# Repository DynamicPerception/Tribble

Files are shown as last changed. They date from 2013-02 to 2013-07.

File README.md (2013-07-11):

Tribble Board
=============

Tribble is the core PCB in the MX3 Motion Controller.

Key Features
------------

 * AT90USB1287 processor with USB OTG
 * 5-Button Interface
 * 2x16 LCD display
 * Dual-optocoupled outputs via 1x TRS jack
 * Four auxiliary I/O ports via 2x TRS jacks
 * MoCoBus Interface
 * Multiple Power Source Inputs

Author
------

The Tribble board was designed and created by Parker Dillmann (longhornengineer)

License and Copyright
---------------------

Tribble and the MX3 are Copyright (c) 2012-2013 Dynamic Perception LLC.

All files shared under the Creative Commons Attibution-Share-Alike 3.0 License.

Tribble and MX3 names are trademarks of Dynamic Perception LLC.

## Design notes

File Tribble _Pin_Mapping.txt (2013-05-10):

MX-3 Pin Mapping 
AT90USB646

0	PA0		M0_A
1	PA1		M0_B
2	PA2		M0_P
3	PA3		M1_A
4	PA4		M1_B
5	PA5		M1_P
6	PA6		M2_A
7	PA7		M2_B

8	PB0		M2_P
9	PB1		SCK
10	PB2		MOSI
11	PB3		MISO
12	PB4		COM1
13	PB5		SHT
14	PB6		N/a
15	PB7		FOC

16	PC0		LCD_D4
17	PC1		LCD_D5
18	PC2		LCD_D6
19	PC3		LCD_D7
20	PC4		LCD_E
21	PC5		LCD_RS
22	PC6		LCD_BK
23	PC7		N/a

24	PD0		COM3
25	PD1		COM2
26	PD2		RX
27	PD3		TX
28	PD4		DE
29	PD5		N/a
30	PD6		N/a
31	PD7		N/a

32	PE0		IO_3
33	PE1		N/a
34	PE2		N/a
35	PE3		OTG USB
36	PE4		IO_0
37	PE5		IO_1
38	PE6		IO_2
39	PE7		UVCON

40	PF0		BTNS
41	PF1		CUR_SENSOR
42	PF2		VOL_SENSOR
43	PF3		TEMP2_SENSOR
44	PF4		TEMP1_SENSOR
45	PF5		TEMP0_SENSOR
46	PF6		N/a
47	PF7		N/a

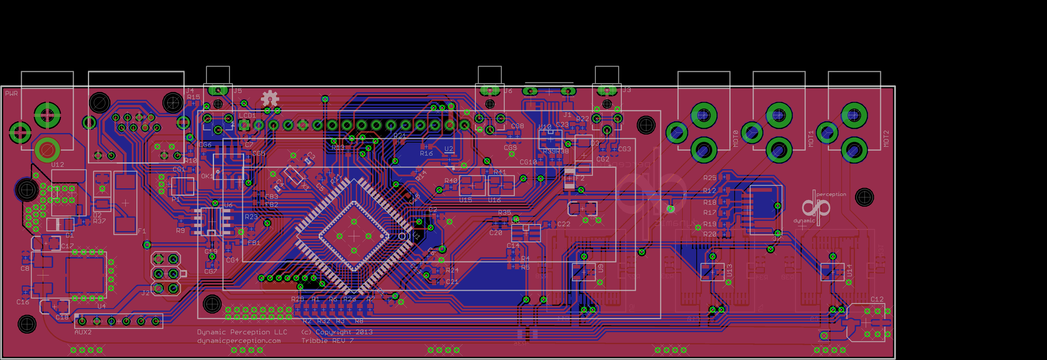
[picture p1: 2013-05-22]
Layout.png

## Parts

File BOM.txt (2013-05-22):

Partlist

Exported from Tribble.sch at 5/22/2013 1:43:17 PM

EAGLE Version 6.2.0 Copyright (c) 1988-2012 CadSoft

Assembly variant: 

Part     Value                    Device                          Package                Library               Sheet

AUX2                              PH_1X06SMALL_PTH                HEADER_01X06_SMALL_PTH PP_Connectors         1
C1       .1uF                     CAP_NONPOL0402                  0402_CAP               parkers_parts         1
C2       .1uF                     CAP_NONPOL0402                  0402_CAP               parkers_parts         1
C3       6pF                      CAP0402                         C0402                  SparkFun              1
C4       6pF                      CAP0402                         C0402                  SparkFun              1
C5       .1uF                     CAP_NONPOL0402                  0402_CAP               parkers_parts         1
C6       .1uF                     CAP_NONPOL0402                  0402_CAP               parkers_parts         1
C7       .1uF                     CAP_NONPOL0402                  0402_CAP               parkers_parts         1
C8       .1uF 35V                 CAP_NONPOL0402                  0402_CAP               parkers_parts         1
C9       .1uF 35V                 CAP_NONPOL0402                  0402_CAP               parkers_parts         1
C10      .1uF 35V                 CAP_NONPOL0402                  0402_CAP               parkers_parts         1
C11      .1uF 35V                 CAP_NONPOL0402                  0402_CAP               parkers_parts         1
C12      100uF                    CAPACITOR_POLARIZED6.3MM_SMD    6.3MM_CAP_SMD          PP_Passives           1
C13      .1uF                     CAP_NONPOL0402                  0402_CAP               parkers_parts         1
C14      .1uF                     CAP_NONPOL0402                  0402_CAP               parkers_parts         1
C15      1uF                      CAP_NONPOL0402                  0402_CAP               parkers_parts         1
C16      .1uF                     CAP_NONPOL0402                  0402_CAP               parkers_parts         1
C17      2.2uF                    CAP_POL1206                     EIA3216                SparkFun              1
C18      10uF                     CAP_POL1206                     EIA3216                SparkFun              1
C19      .1uF                     CAP_NONPOL0402                  0402_CAP               parkers_parts         1
C20      .1uF                     CAP_NONPOL0402                  0402_CAP               parkers_parts         1
C21      .1uF                     CAP_NONPOL0402                  0402_CAP               parkers_parts         1
C22      .1uF                     CAP_NONPOL0402                  0402_CAP               parkers_parts         1
C23      .1uF                     CAP_NONPOL0402                  0402_CAP               parkers_parts         1
C24      10uF                     CAP_POL1206                     EIA3216                SparkFun              1
CG1      B72590D50H260            RESISTOR0402                    0402_RES               parkers_parts         1
CG2      B72590D50H260            RESISTOR0402                    0402_RES               parkers_parts         1
CG3      B72590D50H260            RESISTOR0402                    0402_RES               parkers_parts         1
CG4      B72590D50H260            RESISTOR0402                    0402_RES               parkers_parts         1
CG5      B72590D50H260            RESISTOR0402                    0402_RES               parkers_parts         1
CG6      B72590D50H260            RESISTOR0402                    0402_RES               parkers_parts         1
CG7      B72590D50H260            RESISTOR0402                    0402_RES               parkers_parts         1
CG8      B72590D50H260            RESISTOR0402                    0402_RES               parkers_parts         1
CG9      B72590D50H260            RESISTOR0402                    0402_RES               parkers_parts         1
CG10     B72590D50H260            RESISTOR0402                    0402_RES               parkers_parts         1
D1       MMSZ5240C-V-GS08         DIODESOD-123                    SOD-123                parkers_parts         1
D2       PMEG6010EP,115           DIODESOD-128                    SOD-128                parkers_parts         1
D3       PMEG6010EP,115           DIODESOD-128                    SOD-128                PP_Passives           1
F1       MF-SM050-2-99            PTC_FUSE2920                    2920                   PP_Passives           1
F2       1206L025YR               PTC_FUSE1206                    1206                   PP_Passives           1
FB1      LI0402C470R-10           RESISTOR0402                    0402_RES               parkers_parts         1
FB2      LI0402C470R-10           RESISTOR0402                    0402_RES               parkers_parts         1
FB3      LI0402C470R-10           RESISTOR0402                    0402_RES               parkers_parts         1
J1       10118193-0001LF          USB10118193-0001LF              10118193-0001LF        PP_Connectors         1
J2       68602-406HLF             P2X03                           P2X03                  parkers_parts         1
J3       SJ1-2503A                TRS_STEREO_JACKSJ1-2503A        SJ1-2503A              parkers_parts         1
J4       RJHSE-5381               RJHS-538X                       RIGHT_ANGLE            amphenol ethernet     1
J5       SJ1-2503A                TRS_STEREO_JACKSJ1-2503A        SJ1-2503A              parkers_parts         1
J6       SJ1-2503A                TRS_STEREO_JACKSJ1-2503A        SJ1-2503A              parkers_parts         1
J7       HFW6R-2STE1LF            PH_1X06FFC                      HFW6R-2STE1LF          PP_Connectors         1
LCD1     LCD-16X2NOHOLES          LCD-16X2NOHOLES                 LCD-16X2_NOHOLES       SparkFun-Displays     1
MOT0     KLDX-0202-B-LT           DC_JACKPTH_TIGHT                DC_JACK_PTH_TIGHT      PP_Connectors         1
MOT1     KLDX-0202-B-LT           DC_JACKPTH_TIGHT                DC_JACK_PTH_TIGHT      PP_Connectors         1
MOT2     KLDX-0202-B-LT           DC_JACKPTH_TIGHT                DC_JACK_PTH_TIGHT      PP_Connectors         1
OK1      ACPL-227                 ACPL-227                        SOIC8                  avago-opto            1
P1       TC33X-2                  TC33X-2                         3MMSMD                 bourns trimpot        1
PWR      KLDX-0202-A-LT           DC_JACKPTH_TIGHT                DC_JACK_PTH_TIGHT      PP_Connectors         1
R1       4.7K                     RESISTOR0402                    0402_RES               parkers_parts         1
R2       4.7K                     RESISTOR0402                    0402_RES               parkers_parts         1
R3       4.7K                     RESISTOR0402                    0402_RES               parkers_parts         1
R4       4K                       RESISTOR0402                    0402_RES               parkers_parts         1
R5       20K                      RESISTOR0402                    0402_RES               parkers_parts         1
R6       4.7K                     RESISTOR0402                    0402_RES               parkers_parts         1
R7       4.7K                     RESISTOR0402                    0402_RES               parkers_parts         1
R8       4.7K                     RESISTOR0402                    0402_RES               parkers_parts         1
R9       120                      RESISTOR0402                    0402_RES               parkers_parts         1
R10      330                      RESISTOR0402                    0402_RES               parkers_parts         1
R11      10K                      RESISTOR0402                    0402_RES               parkers_parts         1
R12      500                      RESISTOR0402                    0402_RES               parkers_parts         1
R13      100                      RESISTOR0402                    0402_RES               parkers_parts         1
R14      5K                       RESISTOR0402                    0402_RES               parkers_parts         1
R15      330                      RESISTOR0402                    0402_RES               parkers_parts         1
R16      100                      RESISTOR0402                    0402_RES               parkers_parts         1
R17      500                      RESISTOR0402                    0402_RES               parkers_parts         1
R18      500                      RESISTOR0402                    0402_RES               parkers_parts         1
R19      500                      RESISTOR0402                    0402_RES               parkers_parts         1
R20      500                      RESISTOR0402                    0402_RES               parkers_parts         1
R21      2.6K                     RESISTOR0402                    0402_RES               parkers_parts         1
R22      0                        RESISTOR0402                    0402_RES               parkers_parts         1
R23      5K                       RESISTOR0402                    0402_RES               parkers_parts         1
R24      0                        RESISTOR0402                    0402_RES               parkers_parts         1
R25      10K                      RESISTOR0402                    0402_RES               parkers_parts         1
R26      4.7K                     RESISTOR0402                    0402_RES               parkers_parts         1
R27      10K                      RESISTOR0805                    0805                   PP_Passives           1
R28      10K                      RESISTOR0805                    0805                   PP_Passives           1
R29      4.7K                     RESISTOR0402                    0402_RES               parkers_parts         1
R30      10K                      RESISTOR0805                    0805                   PP_Passives           1
R31      10K                      RESISTOR0805                    0805                   PP_Passives           1
R32      4.7K                     RESISTOR0402                    0402_RES               parkers_parts         1
R33      10K                      RESISTOR0805                    0805                   PP_Passives           1
R34      10K                      RESISTOR0805                    0805                   PP_Passives           1
R35      20K                      RESISTOR0402                    0402_RES               parkers_parts         1
R36      LRF1206-LF-R006JT        RESISTOR1206                    1206                   PP_Passives           1
R37      10K                      RESISTOR0402                    0402_RES               parkers_parts         1
R38      22                       RESISTOR0402                    0402_RES               parkers_parts         1
R39      22                       RESISTOR0402                    0402_RES               parkers_parts         1
R40      100K                     RESISTOR0402                    0402_RES               parkers_parts         1
R41      10K                      RESISTOR0402                    0402_RES               parkers_parts         1
U1       AT90USB1287-MU           AT90USB647-MU                   MLF64                  at90usb               1
U2       MMDT3904                 MMDT3904                        SOT363                 SparkFun-DiscreteSemi 1
U3       BTM7755                  BTM7755PG-DSO-36-29             PG-DSO-36-29           PP_PowerIC            1
U4       MC78M05CDTG              FIXED_VOLTAGE_REGDPAK-3         DPAK-3                 PP_PowerIC            1
U5                                BTM7755PG-DSO-36-29             PG-DSO-36-29           PP_PowerIC            1
U6       ISL8483                  SN65176D                        SO-08                  texas                 1
U7                                BTM7755PG-DSO-36-29             PG-DSO-36-29           PP_PowerIC            1
U8       LMP8640MK-F/NOPB         LMP8640TSOT-6                   TSOT-6                 PP_AnalogIC           1
U9       MCP9701T-E/TT            MCP970XSOT-23-3                 SOT-23-3               PP_Sensors            1
U10      IP4234CZ6                IP4234CZ6SOT-457                SOT-457                PP_Passives           1
U11      AT90USB1287-AU           AT90USB647-AU                   TQFP64                 at90usb               1
U12      FDS6679AZ                MOSFET_P-CHANNEL_SINGLEP3-POWER DSO-8                  PP_DiscreteSemi       1
U13      MCP9701T-E/TT            MCP970XSOT-23-3                 SOT-23-3               PP_Sensors            1
U14      MCP9701T-E/TT            MCP970XSOT-23-3                 SOT-23-3               PP_Sensors            1
U15      BC847BMTF                BJT_NPN_SINGLESOT-23            SOT-23                 PP_DiscreteSemi       1
U16      FDV304P                  MOSFET_P-CHANNEL_SINGLESOT-23   SOT-23                 PP_DiscreteSemi       1
X1       TSX-3225 16.0000MF10U-B0 3.2X2.5MMCRYSTAL                3.2X2.5MM              kyocera-crystals      1

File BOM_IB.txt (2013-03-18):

Partlist

Exported from Input_Board.sch at 3/18/2013 1:31:10 PM

EAGLE Version 6.2.0 Copyright (c) 1988-2012 CadSoft

Assembly variant: 

Part     Value          Device         Package       Library              Sheet

J1       HFW6R-2STE1LF  PH_1X06FFC     HFW6R-2STE1LF PP_Connectors        1
SW1      EVQ-Q2203W     SPSTEVQ-Q2203W EVQ-Q2203W    PP_Electromechanical 1
SW2      EVQ-Q2203W     SPSTEVQ-Q2203W EVQ-Q2203W    PP_Electromechanical 1
SW3      EVQ-Q2203W     SPSTEVQ-Q2203W EVQ-Q2203W    PP_Electromechanical 1
SW4      EVQ-Q2203W     SPSTEVQ-Q2203W EVQ-Q2203W    PP_Electromechanical 1
SW5      EVQ-Q2203W     SPSTEVQ-Q2203W EVQ-Q2203W    PP_Electromechanical 1

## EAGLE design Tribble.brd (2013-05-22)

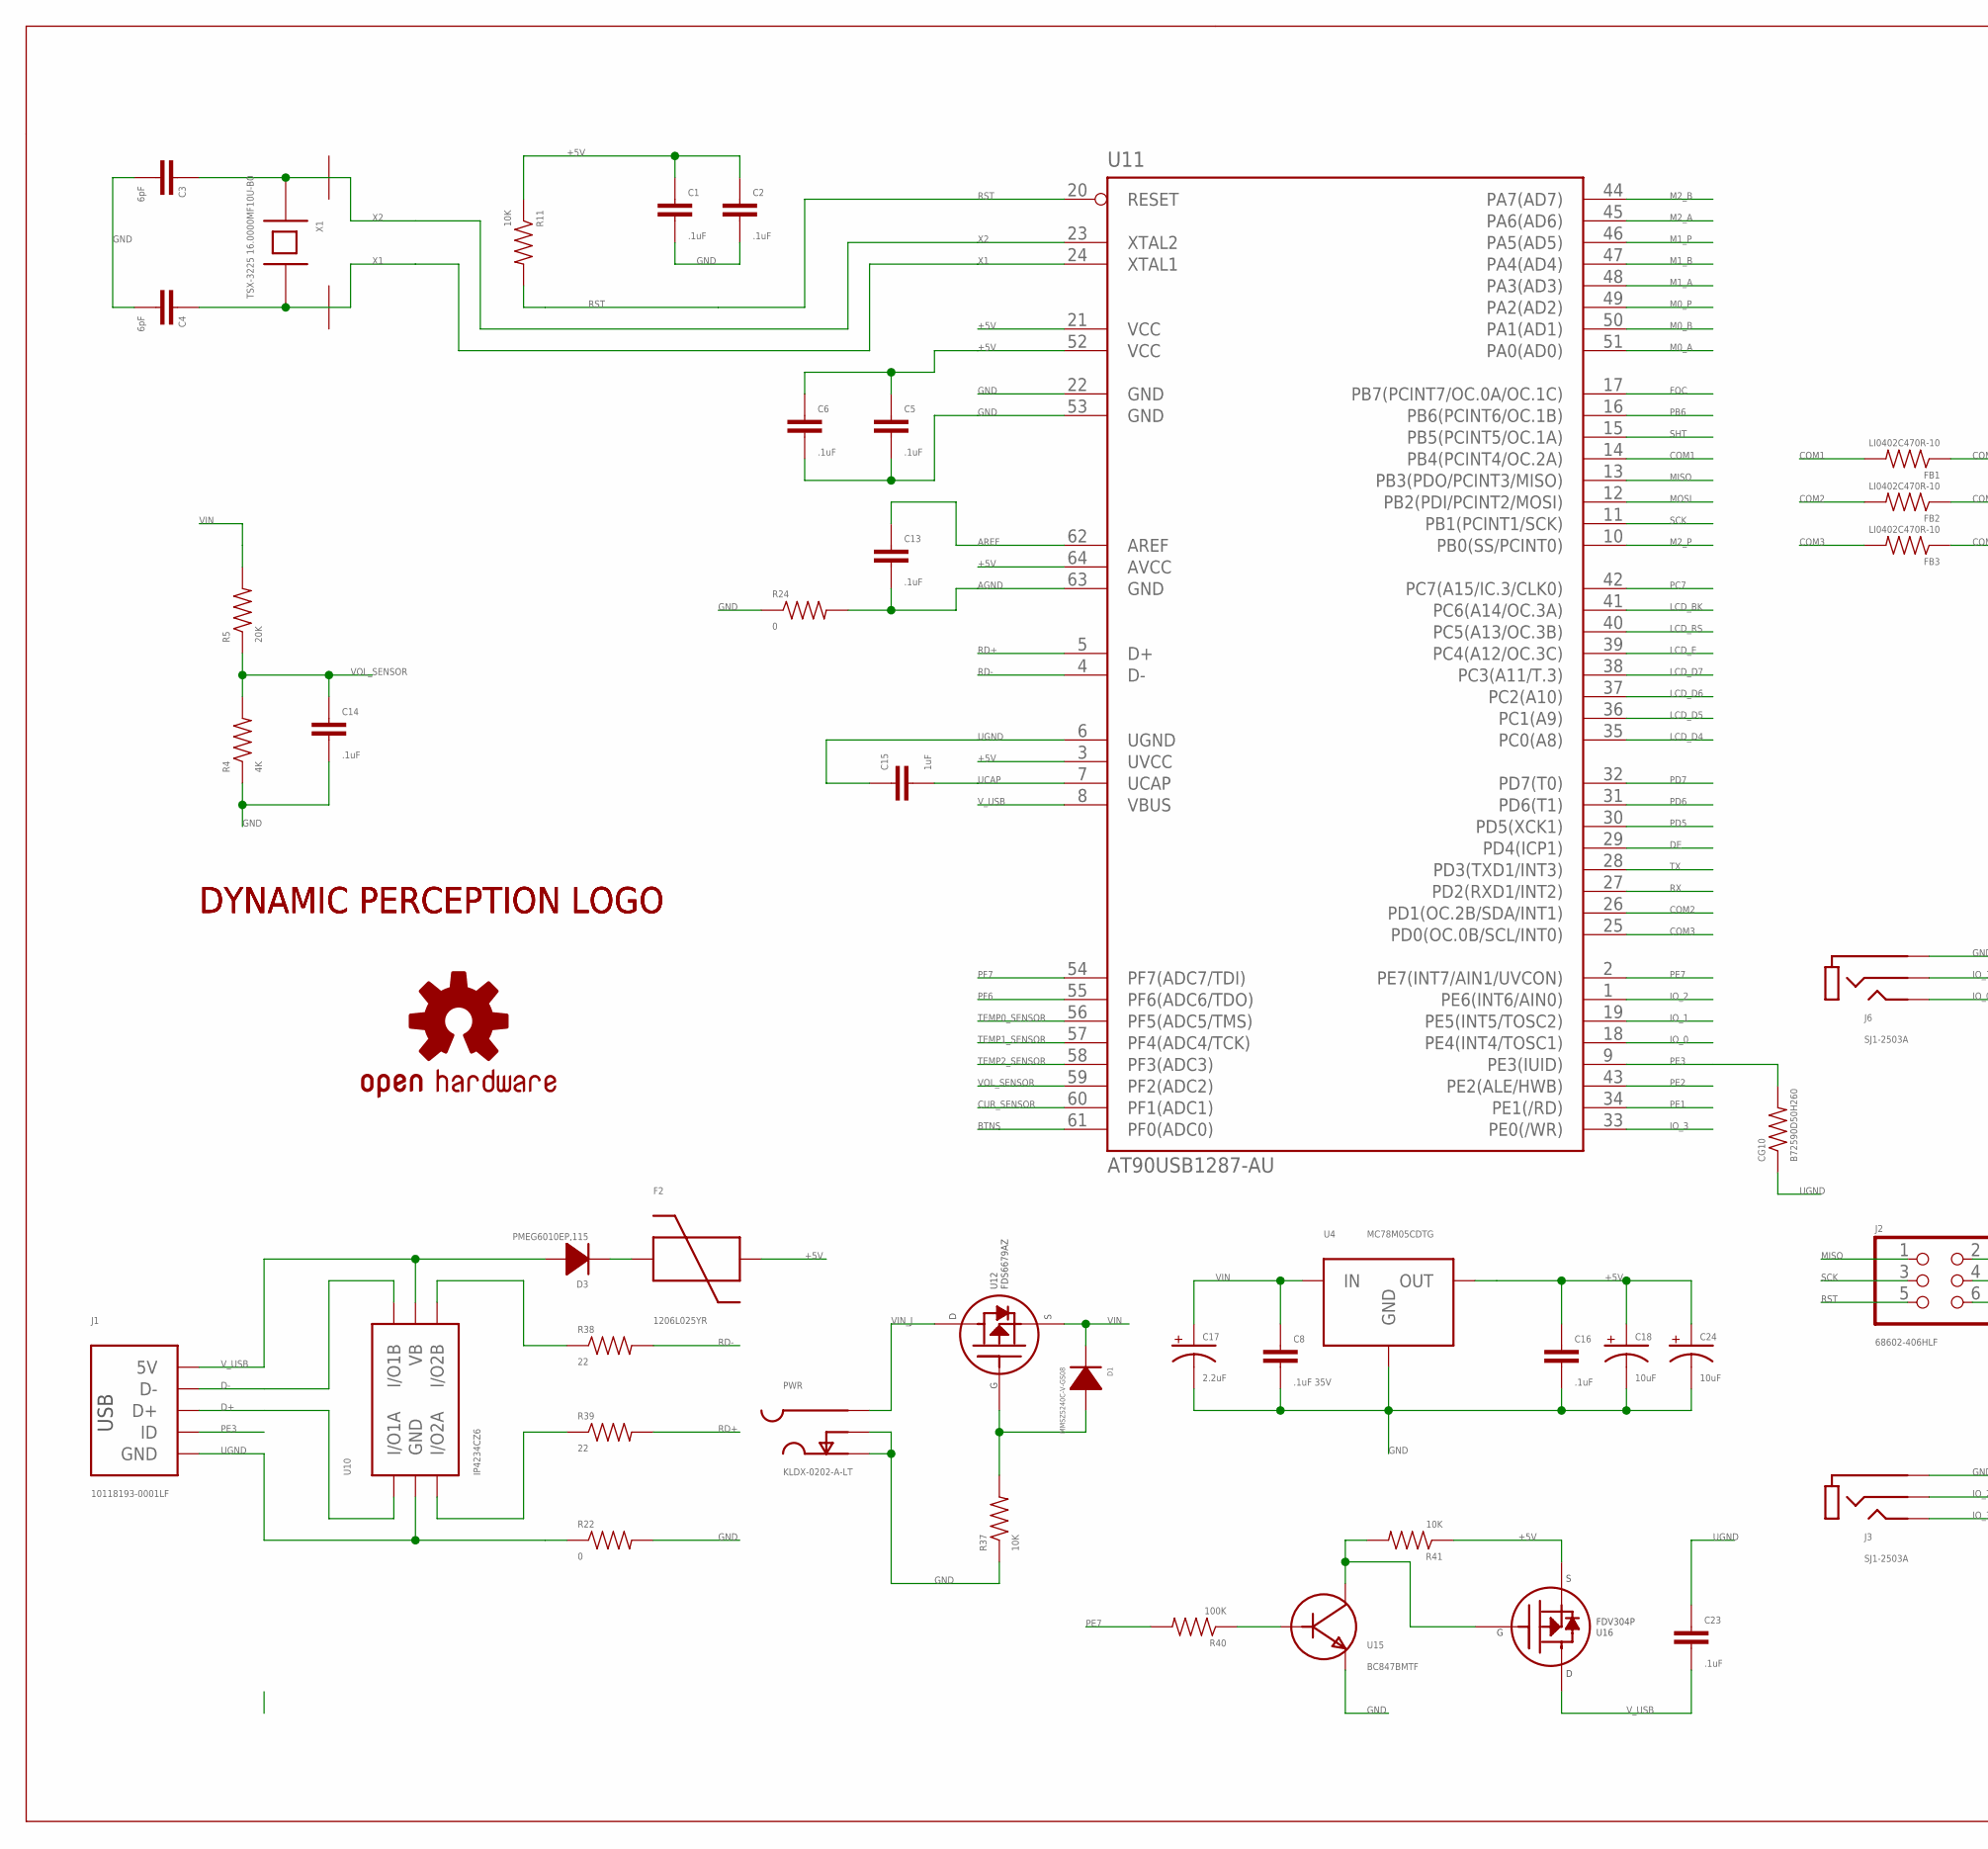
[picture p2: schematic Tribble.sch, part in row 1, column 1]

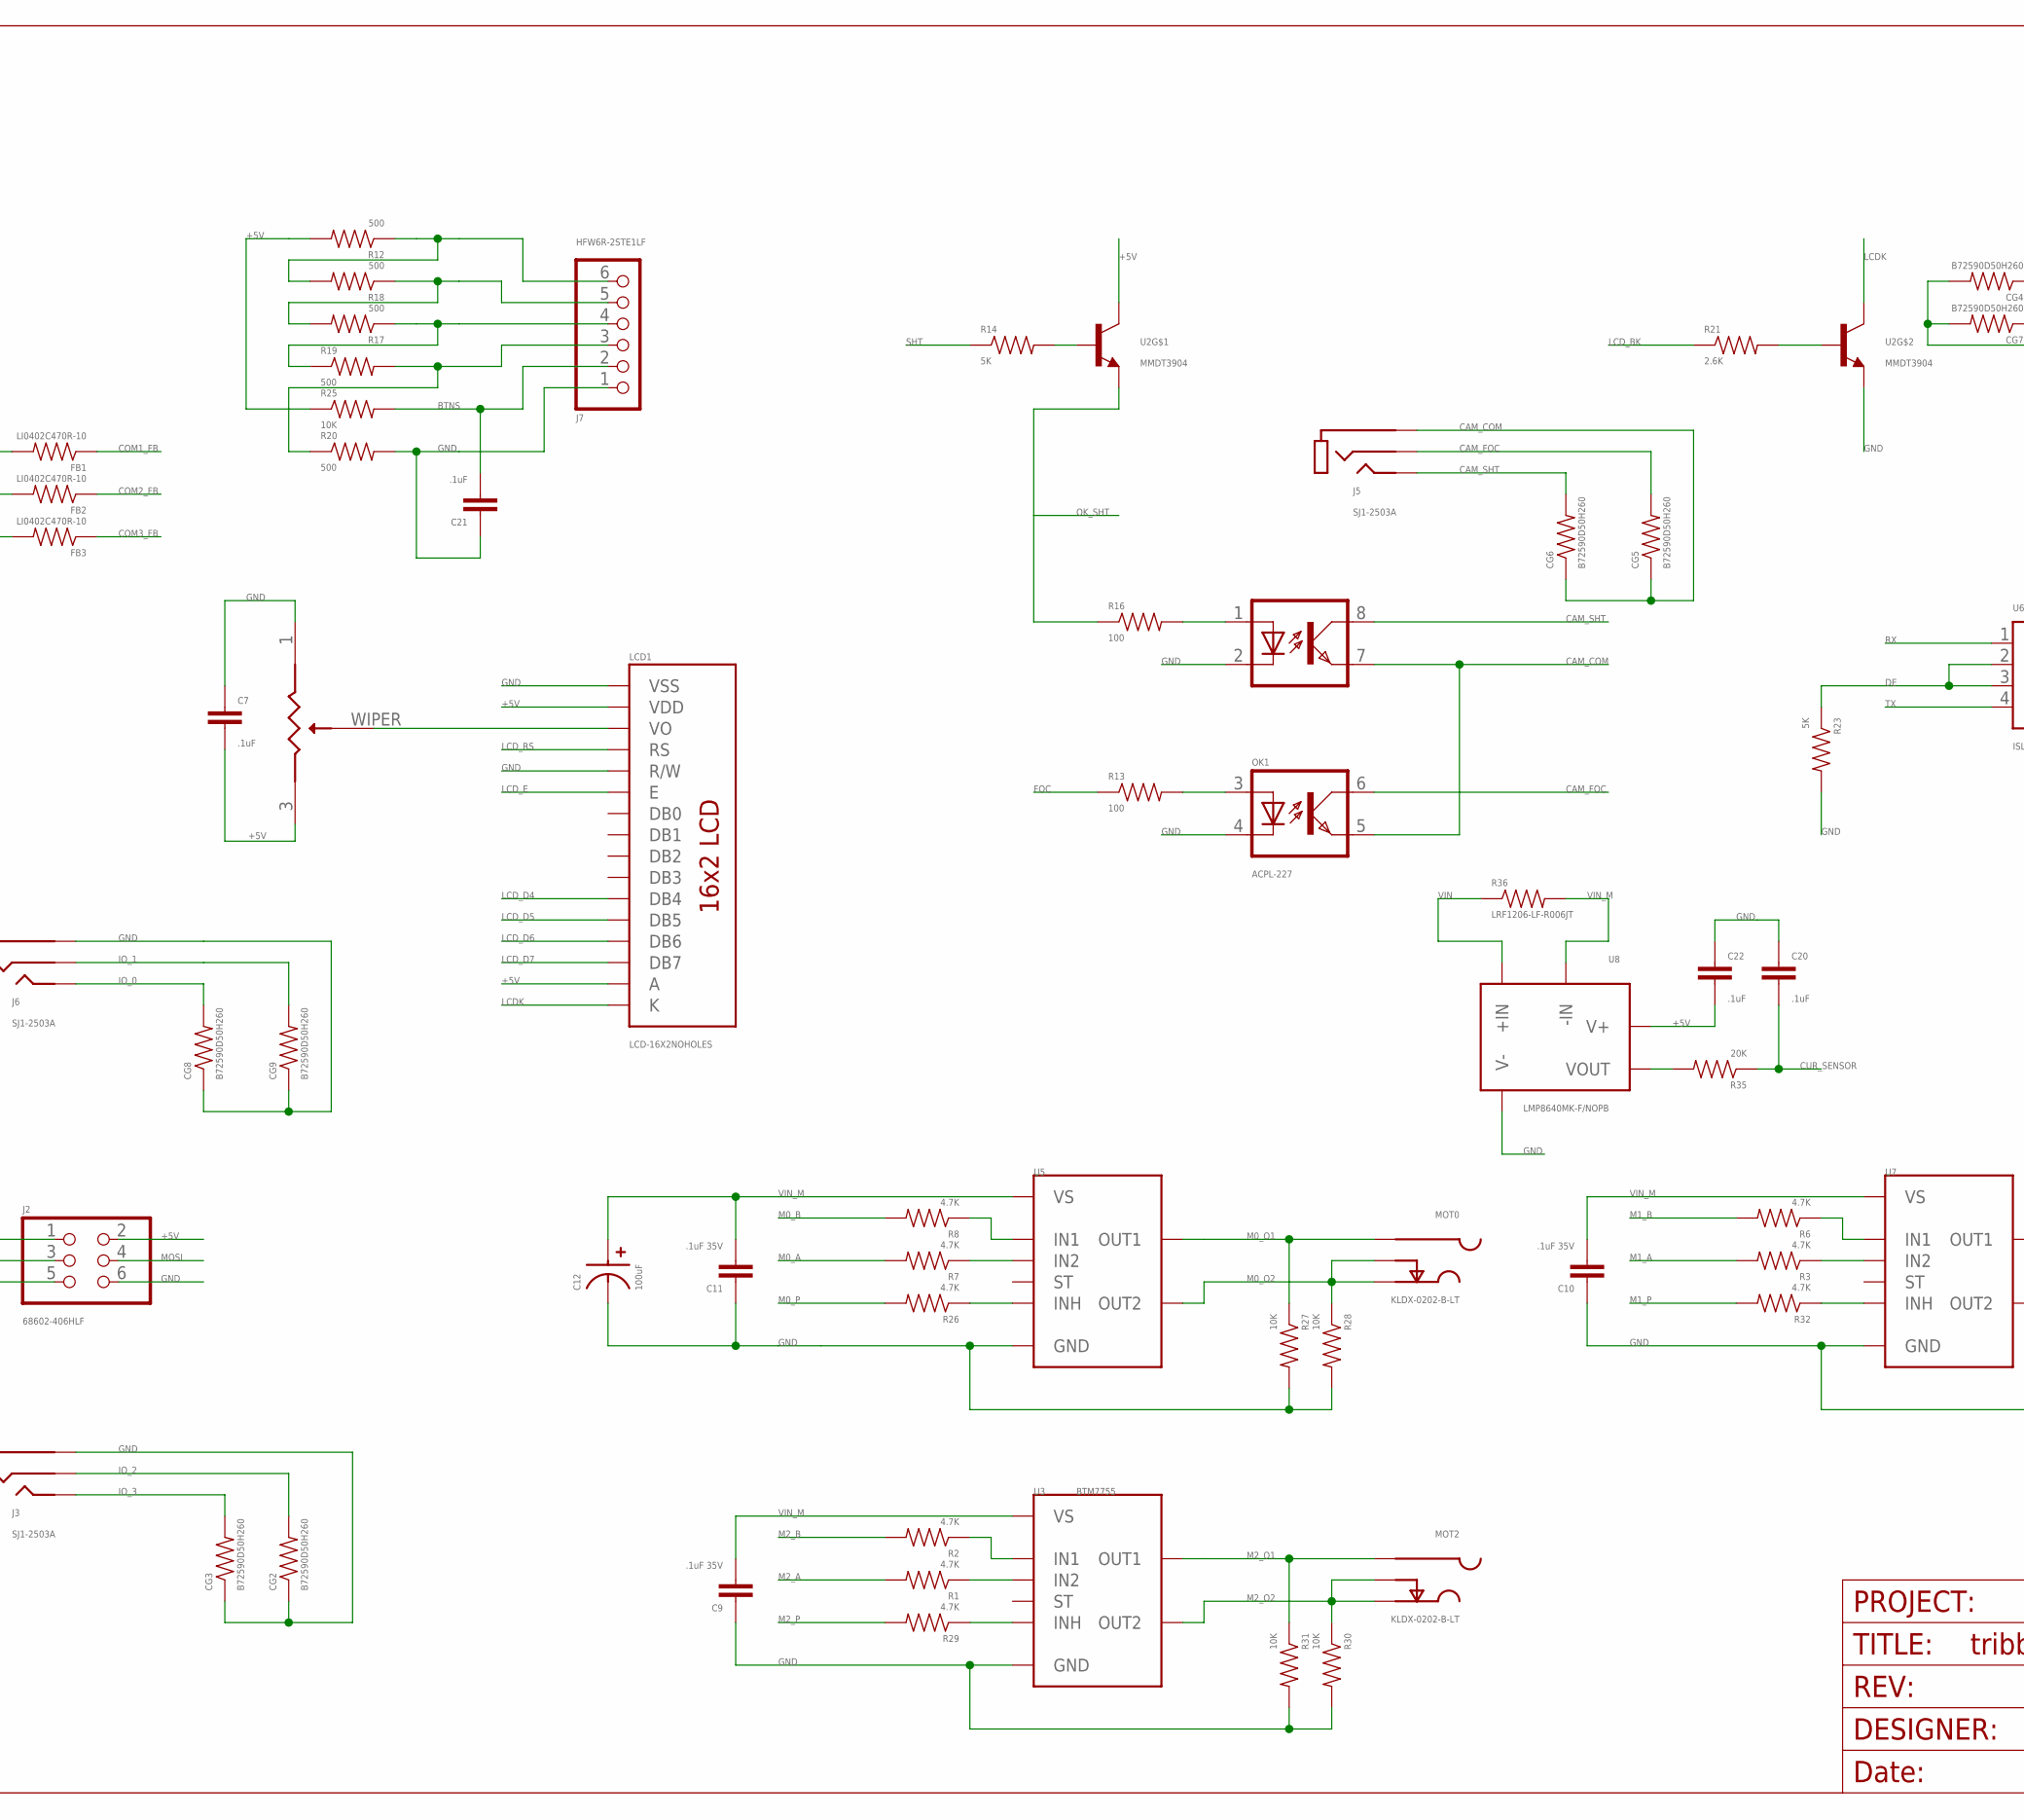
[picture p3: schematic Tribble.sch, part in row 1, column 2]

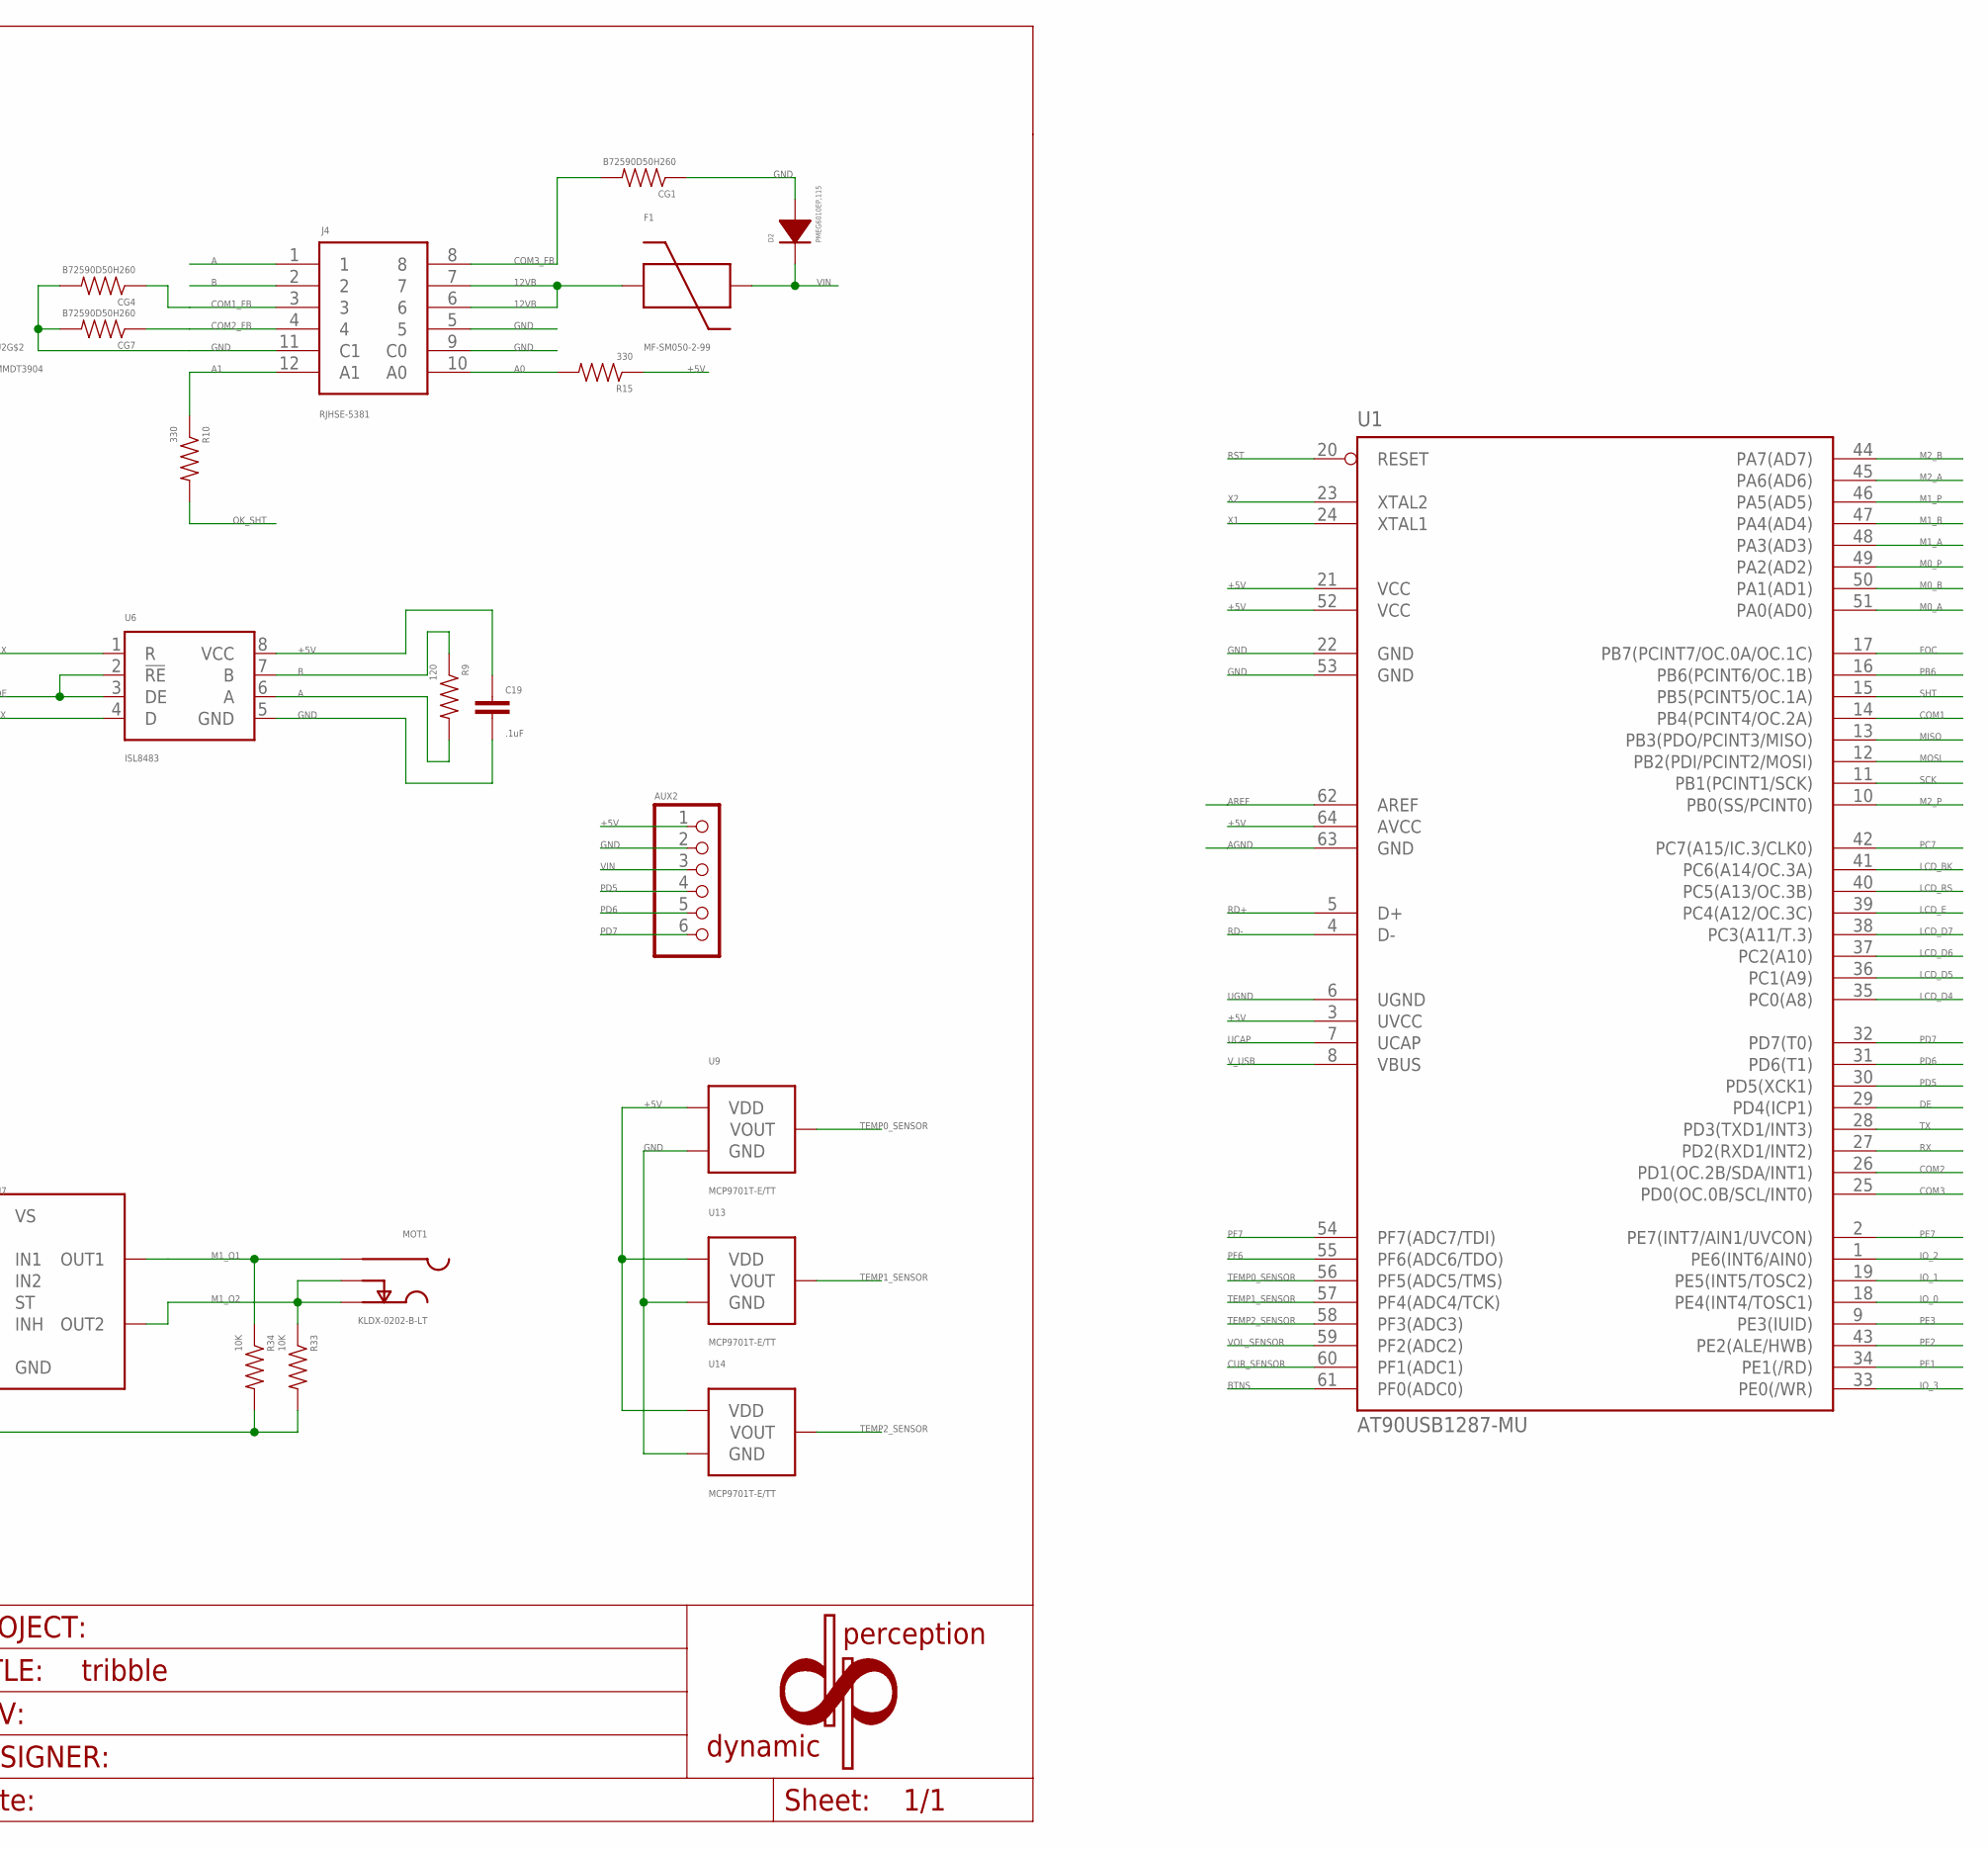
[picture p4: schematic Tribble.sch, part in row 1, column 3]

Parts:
AUX2: PH_1X06SMALL_PTH; HEADER_01X06_SMALL_PTH
C1, C2, C5, C6, C7, C13, C14, C16, C19, C20, C21, C22, C23: .1uF; 0402_CAP
C3, C4: 6pF; C0402
C8, C9, C10, C11: .1uF 35V; 0402_CAP
C12: 100uF; 6.3MM_CAP_SMD
C15: 1uF; 0402_CAP
C17: 2.2uF; EIA3216
C18, C24: 10uF; EIA3216
CG1, CG2, CG3, CG4, CG5, CG6, CG7, CG8, CG9, CG10: B72590D50H260; 0402_RES
D1: MMSZ5240C-V-GS08; SOD-123
D2, D3: PMEG6010EP,115; SOD-128
F1: MF-SM050-2-99; 2920
F2: 1206L025YR; 1206
FB1, FB2, FB3: LI0402C470R-10; 0402_RES
J1: 10118193-0001LF
J2: 68602-406HLF; P2X03
J3, J5, J6: SJ1-2503A
J4: RJHSE-5381; RIGHT_ANGLE
J7: HFW6R-2STE1LF
LCD1: LCD-16X2NOHOLES; LCD-16X2_NOHOLES
LOGO1: DP_LOGOSMALL; DP_LOGO_SMALL
LOGO2: DP_LOGOMICRO; DP_LOGO_MICRO
MOT0, MOT1, MOT2: KLDX-0202-B-LT; DC_JACK_PTH_TIGHT
OK1: ACPL-227; SOIC8
P1: TC33X-2; 3MMSMD
PWR: KLDX-0202-A-LT; DC_JACK_PTH_TIGHT
R1, R2, R3, R6, R7, R8, R26, R29, R32: 4.7K; 0402_RES
R4: 4K; 0402_RES
R5, R35: 20K; 0402_RES
R9: 120; 0402_RES
R10, R15: 330; 0402_RES
R11, R25, R37, R41: 10K; 0402_RES
R12, R17, R18, R19, R20: 500; 0402_RES
R13, R16: 100; 0402_RES
R14, R23: 5K; 0402_RES
R21: 2.6K; 0402_RES
R22, R24: 0; 0402_RES
R27, R28, R30, R31, R33, R34: 10K; 0805
R36: LRF1206-LF-R006JT; 1206
R38, R39: 22; 0402_RES
R40: 100K; 0402_RES
U1: AT90USB1287-MU; MLF64
U2: MMDT3904; SOT363
U3: BTM7755; PG-DSO-36-29
U4: MC78M05CDTG; DPAK-3
U5, U7: BTM7755PG-DSO-36-29; PG-DSO-36-29
U6: ISL8483; SO-08; MPN SN65176BD
U8: LMP8640MK-F/NOPB; TSOT-6
U9, U13, U14: MCP9701T-E/TT; SOT-23-3
U10: IP4234CZ6; SOT-457
U11: AT90USB1287-AU; TQFP64
U12: FDS6679AZ; DSO-8
U15: BC847BMTF; SOT-23
U16: FDV304P; SOT-23
U$1: DP_FRAME
U$2: OSHW-LOGOS; OSHW-LOGO-S
X1: TSX-3225 16.0000MF10U-B0; 3.2X2.5MM

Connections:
4: X1.4
12VB: F1.1, J4.6, J4.7
+5V: AUX2.1, C1.1, C2.1, C5.1, C6.1, C7.2, C16.1, C18.A (+), C19.1, C22.2, C24.A (+), F2.2, J2.2, LCD1.2 (VDD), LCD1.15 (A), P1.3, R11.1, R12.2, R15.1, R25.1, R41.1, U1.3 (UVCC), U1.21 (VCC), U1.52 (VCC), U1.64 (AVCC), U2.3 (C), U4.2 (OUT), U6.8 (VCC), U8.6 (V+), U9.1 (VDD), U11.3 (UVCC), U11.21 (VCC), U11.52 (VCC), U11.64 (AVCC), U13.1 (VDD), U14.1 (VDD), U16.2 (SOURCE)
A: J4.1, R9.2, U6.6 (A)
A0: J4.10 (A0), R15.2
A1: J4.12 (A1), R10.1
AGND: C13.2, R24.2, U1.63 (GND), U11.63 (GND)
AREF: C13.1, U1.62 (AREF), U11.62 (AREF)
B: J4.2, R9.1, U6.7 (B)
BTNS: C21.2, J7.2, R25.2, U1.61 (PF0(ADC0)), U11.61 (PF0(ADC0))
CAM_COM: CG5.1, CG6.1, J5.1 (S), OK1.5 (EMIT1), OK1.7 (EMIT)
CAM_FOC: CG5.2, J5.4 (R), OK1.6 (COL1)
CAM_SHT: CG6.2, J5.2 (T), J5.3 (T), OK1.8 (COL)
COM1: FB1.2, U1.14 (PB4(PCINT4/OC.2A)), U11.14 (PB4(PCINT4/OC.2A))
COM1_FB: CG4.1, FB1.1, J4.3
COM2: FB2.2, U1.26 (PD1(OC.2B/SDA/INT1)), U11.26 (PD1(OC.2B/SDA/INT1))
COM2_FB: CG7.1, FB2.1, J4.4
COM3: FB3.2, U1.25 (PD0(OC.0B/SCL/INT0)), U11.25 (PD0(OC.0B/SCL/INT0))
COM3_FB: CG1.2, FB3.1, J4.8
CUR_SENSOR: C20.2, R35.1, U1.60 (PF1(ADC1)), U11.60 (PF1(ADC1))
D+: J1.3 (D+), U10.1 (I/O1A)
D-: J1.2 (D-), U10.6 (I/O1B)
DE: R23.1, U1.29 (PD4(ICP1)), U6.2 (!RE), U6.3 (DE), U11.29 (PD4(ICP1))
FDV_GATE: R41.2, U15.3 (COLLECTOR), U16.1 (GATE)
FOC: R13.1, U1.17 (PB7(PCINT7/OC.0A/OC.1C)), U11.17 (PB7(PCINT7/OC.0A/OC.1C))
GND: AUX2.2, C1.2, C2.2, C3.1, C4.1, C5.2, C6.2, C7.1, C8.2, C9.1, C10.1, C11.1, C12.NEG, C14.2, C16.2, C17.C (-), C18.C (-), C19.2, C20.1, C21.1, C22.1, C24.C (-), CG1.1, CG2.1, CG3.1, CG4.2, CG7.2, CG8.1, CG9.1, D2.ANODE, J2.6, J3.1 (S), J4.5, J4.9 (C0), J4.11 (C1), J6.1 (S), J7.1, LCD1.1 (VSS), LCD1.5 (R/W), OK1.2 (C), OK1.4 (C1), P1.1, PWR.GND (SLEEVE), PWR.GNDBREAK (SLEEVE_SHUNT), R4.1, R20.2, R22.2, R23.2, R24.1, R27.2, R28.2, R30.2, R31.2, R33.2, R34.2, R37.1, U1.22 (GND), U1.53 (GND), U2.1 (E), U3.5 (GND), U3.6 (GND), U3.7 (GND), U3.8 (GND), U3.23 (GND), U3.24 (GND), U3.25 (GND), U3.26 (GND), U4.4 (GND), U5.5 (GND), U5.6 (GND), U5.7 (GND), U5.8 (GND), U5.23 (GND), U5.24 (GND), U5.25 (GND), U5.26 (GND), U6.5 (GND), U7.5 (GND), U7.6 (GND), U7.7 (GND), U7.8 (GND), U7.23 (GND), U7.24 (GND), U7.25 (GND), U7.26 (GND), U8.2 (V-), U9.3 (GND), U11.22 (GND), U11.53 (GND), U13.3 (GND), U14.3 (GND), U15.2 (EMITTER), X1.2 (GND)
IO_0: CG8.2, J6.2 (T), J6.3 (T), U1.18 (PE4(INT4/TOSC1)), U11.18 (PE4(INT4/TOSC1))
IO_1: CG9.2, J6.4 (R), U1.19 (PE5(INT5/TOSC2)), U11.19 (PE5(INT5/TOSC2))
IO_2: CG2.2, J3.4 (R), U1.1 (PE6(INT6/AIN0)), U11.1 (PE6(INT6/AIN0))
IO_3: CG3.2, J3.2 (T), J3.3 (T), U1.33 (PE0(/WR)), U11.33 (PE0(/WR))
LCDK: LCD1.16 (K), U2.6 (C)
LCD_BK: R21.1, U1.41 (PC6(A14/OC.3A)), U11.41 (PC6(A14/OC.3A))
LCD_D4: LCD1.11 (DB4), U1.35 (PC0(A8)), U11.35 (PC0(A8))
LCD_D5: LCD1.12 (DB5), U1.36 (PC1(A9)), U11.36 (PC1(A9))
LCD_D6: LCD1.13 (DB6), U1.37 (PC2(A10)), U11.37 (PC2(A10))
LCD_D7: LCD1.14 (DB7), U1.38 (PC3(A11/T.3)), U11.38 (PC3(A11/T.3))
LCD_E: LCD1.6 (E), U1.39 (PC4(A12/OC.3C)), U11.39 (PC4(A12/OC.3C))
LCD_RS: LCD1.4 (RS), U1.40 (PC5(A13/OC.3B)), U11.40 (PC5(A13/OC.3B))
M0_A: R7.2, U1.51 (PA0(AD0)), U11.51 (PA0(AD0))
M0_A1: R7.1, U5.10 (IN2)
M0_B: R8.2, U1.50 (PA1(AD1)), U11.50 (PA1(AD1))
M0_B1: R8.1, U5.9 (IN1)
M0_O1: MOT0.PWR (PIN), R27.1, U5.1 (OUT1), U5.2 (OUT1), U5.3 (OUT1), U5.4 (OUT1), U5.33 (OUT1), U5.34 (OUT1), U5.35 (OUT1), U5.36 (OUT1)
M0_O2: MOT0.GND (SLEEVE), MOT0.GNDBREAK (SLEEVE_SHUNT), R28.1, U5.15 (OUT2), U5.16 (OUT2), U5.17 (OUT2), U5.18 (OUT2), U5.19 (OUT2), U5.20 (OUT2), U5.21 (OUT2), U5.22 (OUT2)
M0_P: R26.2, U1.49 (PA2(AD2)), U11.49 (PA2(AD2))
M0_P1: R26.1, U5.27 (INH)
M1_A: R3.2, U1.48 (PA3(AD3)), U11.48 (PA3(AD3))
M1_B: R6.2, U1.47 (PA4(AD4)), U11.47 (PA4(AD4))
M1_O1: MOT1.PWR (PIN), R34.1, U7.1 (OUT1), U7.2 (OUT1), U7.3 (OUT1), U7.4 (OUT1), U7.33 (OUT1), U7.34 (OUT1), U7.35 (OUT1), U7.36 (OUT1)
M1_O2: MOT1.GND (SLEEVE), MOT1.GNDBREAK (SLEEVE_SHUNT), R33.1, U7.15 (OUT2), U7.16 (OUT2), U7.17 (OUT2), U7.18 (OUT2), U7.19 (OUT2), U7.20 (OUT2), U7.21 (OUT2), U7.22 (OUT2)
M1_P: R32.2, U1.46 (PA5(AD5)), U11.46 (PA5(AD5))
M2_A: R1.2, U1.45 (PA6(AD6)), U11.45 (PA6(AD6))
M2_B: R2.2, U1.44 (PA7(AD7)), U11.44 (PA7(AD7))
M2_O1: MOT2.PWR (PIN), R31.1, U3.1 (OUT1), U3.2 (OUT1), U3.3 (OUT1), U3.4 (OUT1), U3.33 (OUT1), U3.34 (OUT1), U3.35 (OUT1), U3.36 (OUT1)
M2_O2: MOT2.GND (SLEEVE), MOT2.GNDBREAK (SLEEVE_SHUNT), R30.1, U3.15 (OUT2), U3.16 (OUT2), U3.17 (OUT2), U3.18 (OUT2), U3.19 (OUT2), U3.20 (OUT2), U3.21 (OUT2), U3.22 (OUT2)
M2_P: R29.2, U1.10 (PB0(SS/PCINT0)), U11.10 (PB0(SS/PCINT0))
MISO: J2.1, U1.13 (PB3(PDO/PCINT3/MISO)), U11.13 (PB3(PDO/PCINT3/MISO))
MOSI: J2.4, U1.12 (PB2(PDI/PCINT2/MOSI)), U11.12 (PB2(PDI/PCINT2/MOSI))
unnamed: R35.2, U8.1 (VOUT)
unnamed: D1.ANODE, R37.2, U12.4 (GATE)
unnamed: R3.1, U7.10 (IN2)
unnamed: R21.2, U2.2 (B)
unnamed: R6.1, U7.9 (IN1)
unnamed: R32.1, U7.27 (INH)
unnamed: R29.1, U3.27 (INH)
unnamed: R2.1, U3.9 (IN1)
unnamed: R1.1, U3.10 (IN2)
unnamed: R38.1, U10.4 (I/O2B)
unnamed: R39.1, U10.3 (I/O2A)
unnamed: D3.CATHODE, F2.1
unnamed: LCD1.3 (VO), P1.WIPER (2)
unnamed: OK1.3 (A1), R13.2
unnamed: OK1.1 (A), R16.2
unnamed: R14.2, U2.5 (B)
unnamed: J7.6, R12.1, R18.2
unnamed: J7.4, R17.1, R19.1
unnamed: J7.5, R17.2, R18.1
unnamed: J7.3, R19.2, R20.1
OK_SHT: R10.2, R16.1, U2.4 (E)
PB6: U1.16 (PB6(PCINT6/OC.1B)), U11.16 (PB6(PCINT6/OC.1B))
PC7: U1.42 (PC7(A15/IC.3/CLK0)), U11.42 (PC7(A15/IC.3/CLK0))
PD5: AUX2.4, U1.30 (PD5(XCK1)), U11.30 (PD5(XCK1))
PD6: AUX2.5, U1.31 (PD6(T1)), U11.31 (PD6(T1))
PD7: AUX2.6, U1.32 (PD7(T0)), U11.32 (PD7(T0))
PE1: U1.34 (PE1(/RD)), U11.34 (PE1(/RD))
PE2: U1.43 (PE2(ALE/HWB)), U11.43 (PE2(ALE/HWB))
PE3: CG10.2, J1.4 (ID), U1.9 (PE3(IUID)), U11.9 (PE3(IUID))
PE7: R40.2, U1.2 (PE7(INT7/AIN1/UVCON)), U11.2 (PE7(INT7/AIN1/UVCON))
PE7_GATE: R40.1, U15.1 (BASE)
PF6: U1.55 (PF6(ADC6/TDO)), U11.55 (PF6(ADC6/TDO))
PF7: U1.54 (PF7(ADC7/TDI)), U11.54 (PF7(ADC7/TDI))
RD+: R39.2, U1.5 (D+), U11.5 (D+)
RD-: R38.2, U1.4 (D-), U11.4 (D-)
RST: J2.5, R11.2, U1.20 (RESET), U11.20 (RESET)
RX: U1.27 (PD2(RXD1/INT2)), U6.1 (R), U11.27 (PD2(RXD1/INT2))
SCK: J2.3, U1.11 (PB1(PCINT1/SCK)), U11.11 (PB1(PCINT1/SCK))
SHT: R14.1, U1.15 (PB5(PCINT5/OC.1A)), U11.15 (PB5(PCINT5/OC.1A))
TEMP0_SENSOR: U1.56 (PF5(ADC5/TMS)), U9.2 (VOUT), U11.56 (PF5(ADC5/TMS))
TEMP1_SENSOR: U1.57 (PF4(ADC4/TCK)), U11.57 (PF4(ADC4/TCK)), U13.2 (VOUT)
TEMP2_SENSOR: U1.58 (PF3(ADC3)), U11.58 (PF3(ADC3)), U14.2 (VOUT)
TX: U1.28 (PD3(TXD1/INT3)), U6.4 (D), U11.28 (PD3(TXD1/INT3))
UCAP: C15.2, U1.7 (UCAP), U11.7 (UCAP)
UGND: C15.1, C23.1, CG10.1, J1.5 (GND), J1.S1 (GND), J1.S2 (GND), J1.S3 (GND), J1.S4 (GND), R22.1, U1.6 (UGND), U10.2 (GND), U11.6 (UGND)
VIN: AUX2.3, C8.1, C17.A (+), D1.CATHODE, D2.CATHODE, F1.2, R5.2, R36.1, U4.1 (IN), U8.3 (+IN), U12.1 (SOURCE), U12.2 (SOURCE), U12.3 (SOURCE)
VIN_J: PWR.PWR (PIN), U12.5 (DRAIN), U12.6 (DRAIN), U12.7 (DRAIN), U12.8 (DRAIN)
VIN_M: C9.2, C10.2, C11.2, C12.POS, R36.2, U3.11 (VS), U3.12 (VS), U3.13 (VS), U3.14 (VS), U3.29 (VS), U3.30 (VS), U3.31 (VS), U3.32 (VS), U5.11 (VS), U5.12 (VS), U5.13 (VS), U5.14 (VS), U5.29 (VS), U5.30 (VS), U5.31 (VS), U5.32 (VS), U7.11 (VS), U7.12 (VS), U7.13 (VS), U7.14 (VS), U7.29 (VS), U7.30 (VS), U7.31 (VS), U7.32 (VS), U8.4 (-IN)
VOL_SENSOR: C14.1, R4.2, R5.1, U1.59 (PF2(ADC2)), U11.59 (PF2(ADC2))
V_USB: C23.2, D3.ANODE, J1.1 (5V), U1.8 (VBUS), U10.5 (VB), U11.8 (VBUS), U16.3 (DRAIN)
X1: C4.2, U1.24 (XTAL1), U11.24 (XTAL1), X1.3
X2: C3.2, U1.23 (XTAL2), U11.23 (XTAL2), X1.1

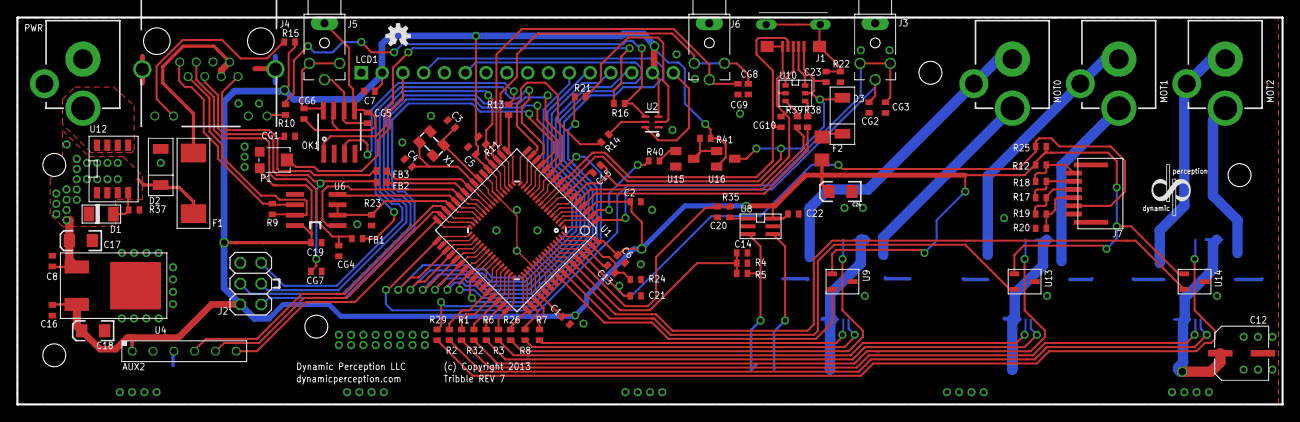
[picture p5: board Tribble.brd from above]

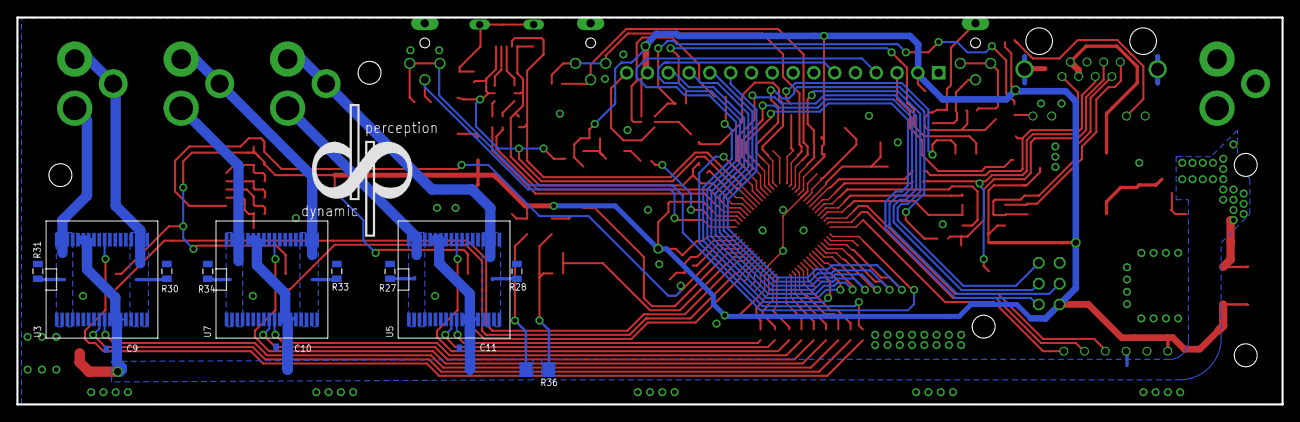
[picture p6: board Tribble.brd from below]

Board: 2 copper layers, 154.5 x 47.2 mm, 119 parts (14 on the bottom side), 109 nets.

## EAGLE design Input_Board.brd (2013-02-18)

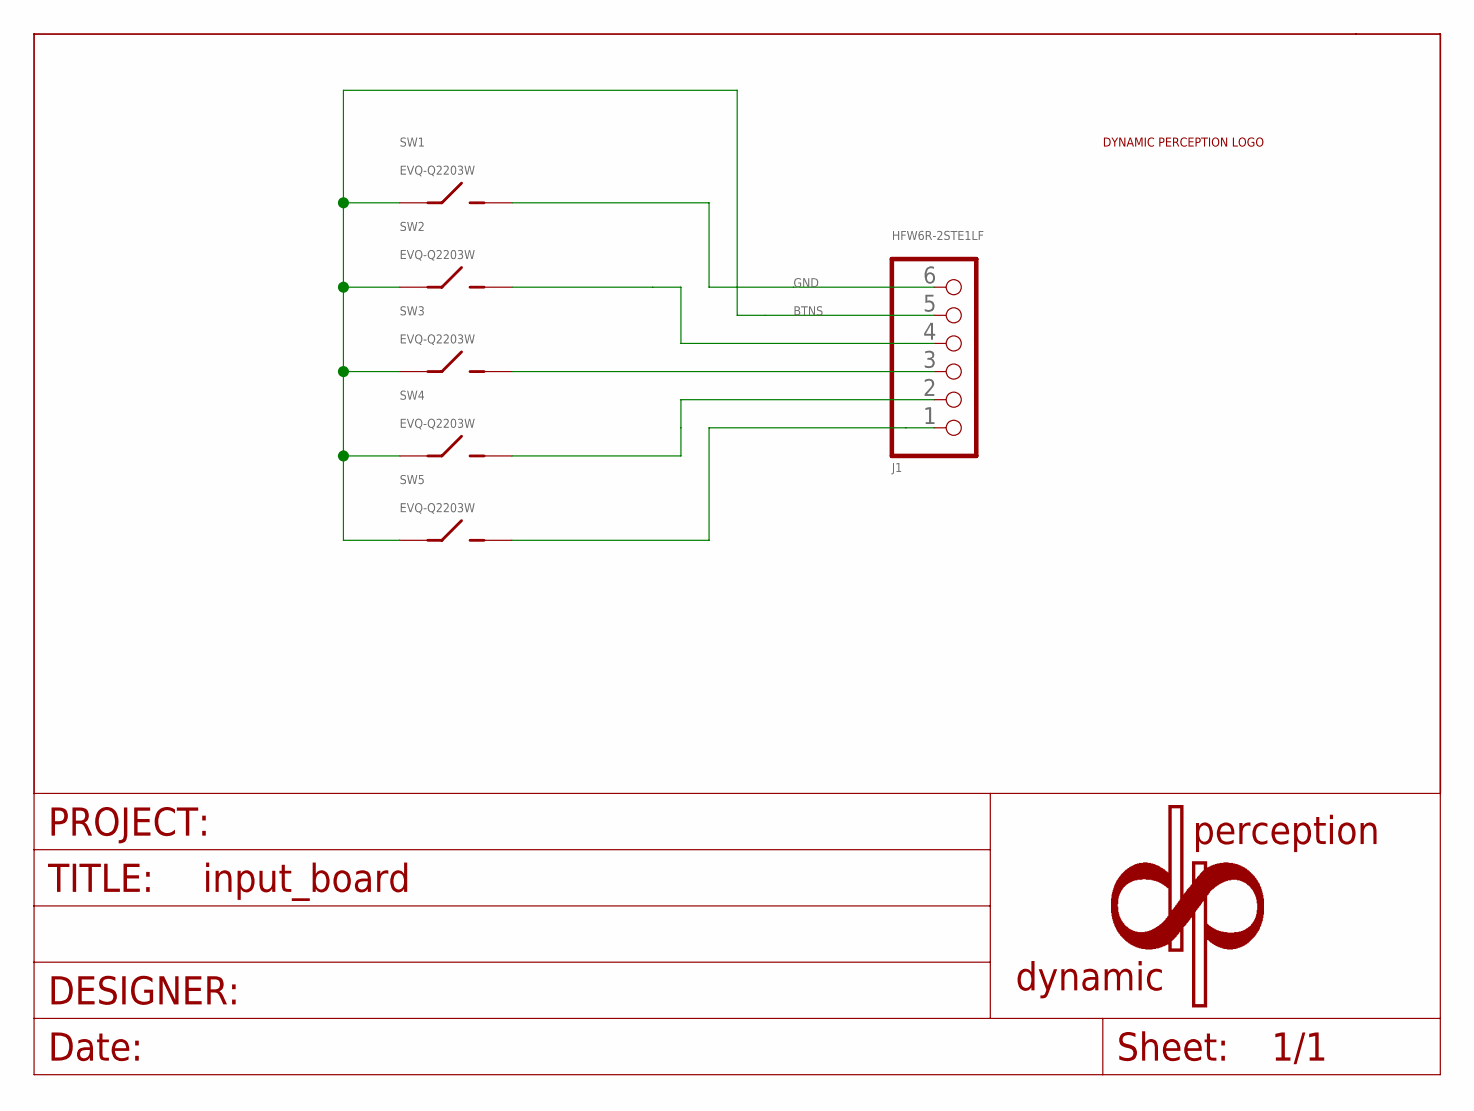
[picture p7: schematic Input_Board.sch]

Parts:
FRAME1: DYNAMIC_PERCEPTION_FRAMEPCB_INFO; DYNAMIC_PERCEPTION_FRAME
J1: HFW6R-2STE1LF
LOGO2: DYNAMIC_PERCEPTION_LOGOMICRO; DP_LOGO_MICRO
SW1, SW2, SW3, SW4, SW5: EVQ-Q2203W

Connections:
BTNS: J1.5, SW1.1 (A), SW1.2 (A), SW2.1 (A), SW2.2 (A), SW3.1 (A), SW3.2 (A), SW4.1 (A), SW4.2 (A), SW5.1 (A), SW5.2 (A)
GND: J1.6, SW1.3 (B), SW1.4 (B)
unnamed: J1.4, SW2.3 (B), SW2.4 (B)
unnamed: J1.3, SW3.3 (B), SW3.4 (B)
unnamed: J1.2, SW4.3 (B), SW4.4 (B)
unnamed: J1.1, SW5.3 (B), SW5.4 (B)

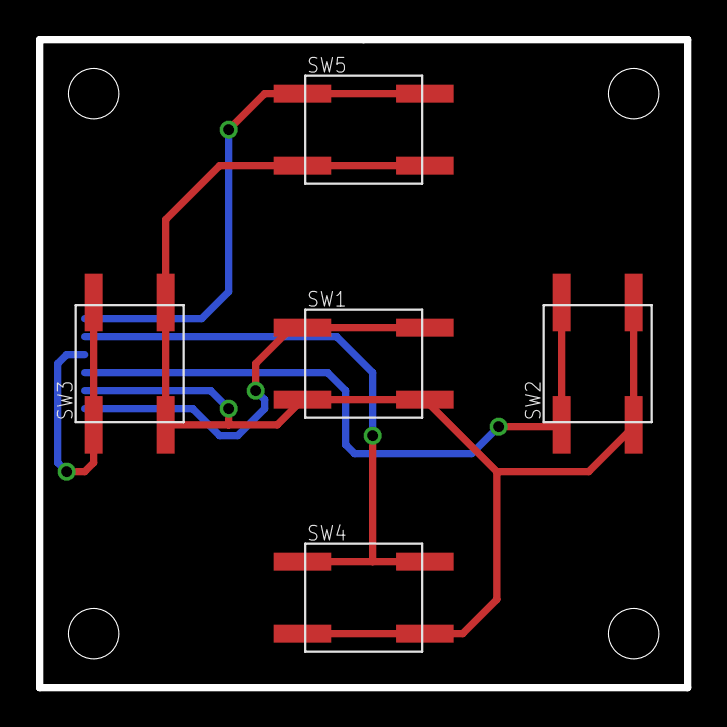
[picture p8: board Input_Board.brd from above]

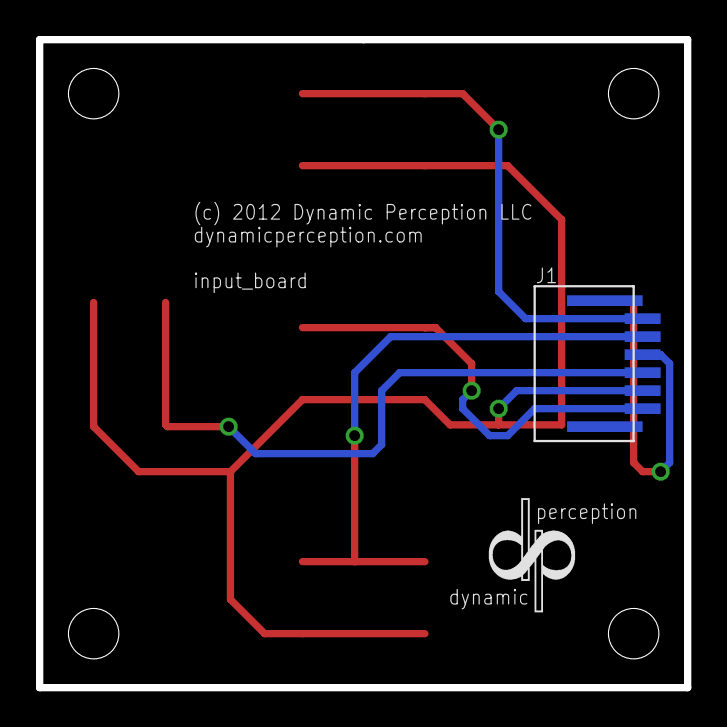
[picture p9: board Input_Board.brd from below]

Board: 2 copper layers, 36.0 x 36.0 mm, 8 parts (3 on the bottom side), 6 nets.

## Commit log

2012-11-21 readding trunk
    [Super_Dolly_Board.brd, Super_Dolly_Board.sch, superdollyboard.skp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]
2012-11-21 checking in changed to the SDB and adding 2 libraries
    [Super_Dolly_Board.brd, Super_Dolly_Board.sch]
2012-11-26 finished routing. needs optimizing for SDB
    [Super_Dolly_Board.brd, Super_Dolly_Board.sch]
2012-11-28 added jumper to bridge VUSB and +5V so the usb can power the device for testing
    [Super_Dolly_Board.brd]
2012-11-29 finished SDB REV2
    [Super_Dolly_Board.brd, Super_Dolly_Board.sch]
2012-12-03 finished REV2 of SDB
    [Super_Dolly_Board.brd, Super_Dolly_Board.sch, superdollyboard.skp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]
2012-12-04 added digital pin numbers to the SDB pin mapping
2013-01-03 REV 3 of SDB in works. Fixed the pull up on the BTNS, changes RS485 chip to one with ESD built in.
    [Super_Dolly_Board.brd, Super_Dolly_Board.sch]
2013-01-11 REV 7 of the USB Board done. Moving to production on it.
    SDB Rev 3 almost done. OTG USB added. Motor controllers switched to BTM7755 to reduce the Resistance on of the drivers.
    [Super_Dolly_Board.brd, Super_Dolly_Board.sch]
2013-01-15 added 0805 package to pp_passives for resistors. changed resistors on the motor output lines from 0402 to 0805 for better heat dissipation.
    [Super_Dolly_Board.brd, Super_Dolly_Board.sch]
2013-01-15 updated cam files for trunk (REV3) of the Super Dolly Board
    [Super_Dolly_Board.brd]
2013-01-18 Tagged SDB REV_3
    [Super_Dolly_Board.brd, Super_Dolly_Board.sch]
2013-02-04 working on SDB REV4
    [Super_Dolly_Board.brd, Super_Dolly_Board.sch]
2013-02-05 working on REv 4 of SDB
    [Super_Dolly_Board.brd, Super_Dolly_Board.sch]
2013-02-06 added a new PP_Sensor library and more parts to the datasheets
    [Super_Dolly_Board.brd, Super_Dolly_Board.sch]
2013-02-07 REV4 of SDB complete. added 2 parts to datasheets and libraires.
    [Super_Dolly_Board.brd, Super_Dolly_Board.sch]
2013-02-08 added a part to PP_poweric and replaced the switcher regulator with a linear one.
    [Super_Dolly_Board.brd, Super_Dolly_Board.sch]
2013-02-12 changed ESD protection to TPD1E10B06DPYR
    [Super_Dolly_Board.brd, Super_Dolly_Board.sch]
2013-02-18 added input board
    [Input_Board.brd, Input_Board.sch, Super_Dolly_Board.brd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]
2013-02-22 fixed a part number issue
    [Super_Dolly_Board.brd, Super_Dolly_Board.sch]
2013-03-18 Fixed some small isues with the SDM REV4 and tagged it as REV5. Added the spreadsheet BOM.
    [Super_Dolly_Board.brd, Super_Dolly_Board.sch]
2013-03-20 Sketchup and DXF of the SDB
    [Super_Dolly_Board.brd]
2013-04-01 added FAB checklists for USB->RS485 and SDB
    [SuperDolly Board PCB FAB Engineering CheckList.xlsx]
2013-04-24 Changed name of SDB to Tribel. Camfiles for Reg Volt Booster added.
    [Trible PCB FAB Engineering CheckList.xlsx, Trible.brd, Trible.sch]
2013-04-24 Changed the name of "tribel" to "tribble" cause I don't watch star trek.
    [SuperDolly Board PCB FAB Engineering CheckList.xlsx, Super_Dolly_Board.brd, Super_Dolly_Board.sch]
2013-04-24 Adding new cam files for Tribble
    [Tribble.brd, Tribble.sch]
2013-04-24 removing old files
    [Trible PCB FAB Engineering CheckList.xlsx, Trible.brd, Trible.sch]
2013-04-25 Finished RVB REV0
    [Tribble.brd]
2013-04-26 fixed minor issues with REV6.
    [Tribble.brd, Tribble.sch]
2013-05-10 Fixing EMC problems with Tribble. Moved lots of traces. Added Ferrite beads to COM1, COM2, Com3. Added proper support for USB OTG
    [Tribble.brd, Tribble.sch]
2013-05-13 tagged REV_7 of Tribble
    [Tribble.brd]
2013-05-22 updated the BOM info for Tribble Rev 7
    [Tribble.brd, Tribble.sch]
2013-06-07 Fixed the issues for Tribble that popped up during EMC testing
    [Tribble.brd, Tribble.sch]
2013-07-03 tagged loads of PCBs and made sure BOMs where up to date
    [Tribble.brd, Tribble.sch]
2013-08-08 Revert to REV 7 of Tribble
    Did not need the board fixes in REV 8 of the pcb.
    [Tribble.brd, Tribble.sch]

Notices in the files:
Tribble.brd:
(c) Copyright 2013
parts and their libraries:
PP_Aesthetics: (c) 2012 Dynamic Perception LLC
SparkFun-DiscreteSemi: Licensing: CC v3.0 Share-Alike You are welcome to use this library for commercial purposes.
